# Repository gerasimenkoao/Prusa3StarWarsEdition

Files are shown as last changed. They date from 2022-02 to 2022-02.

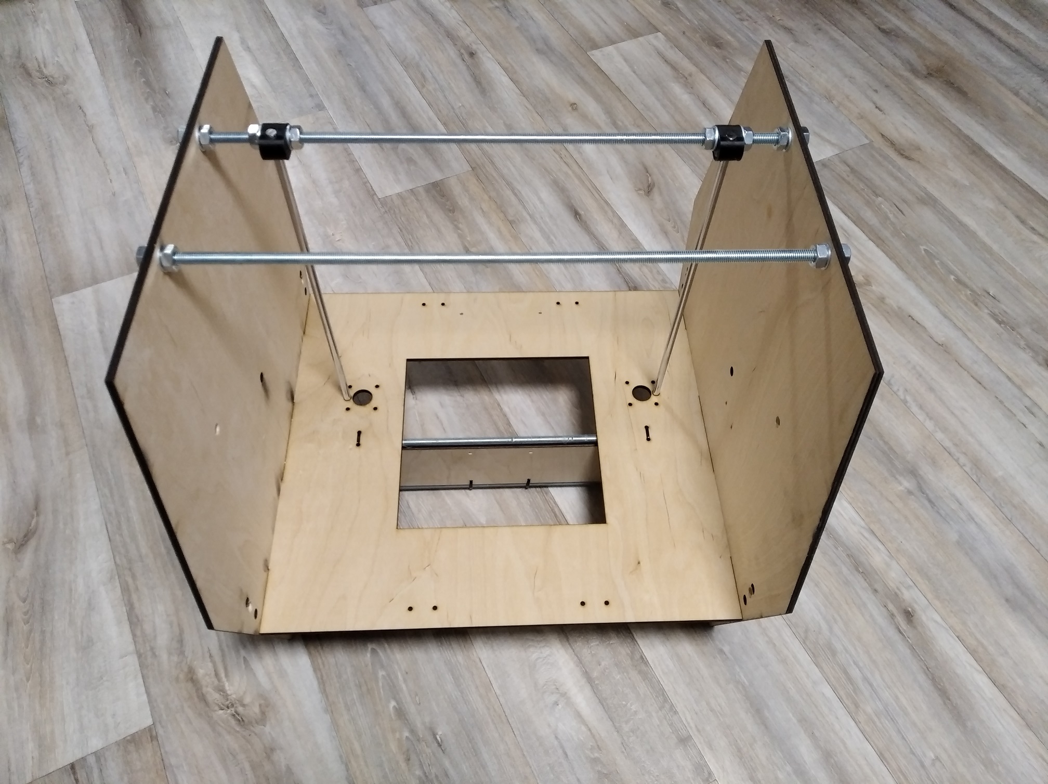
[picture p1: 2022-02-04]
photos/02frameBuild.jpg

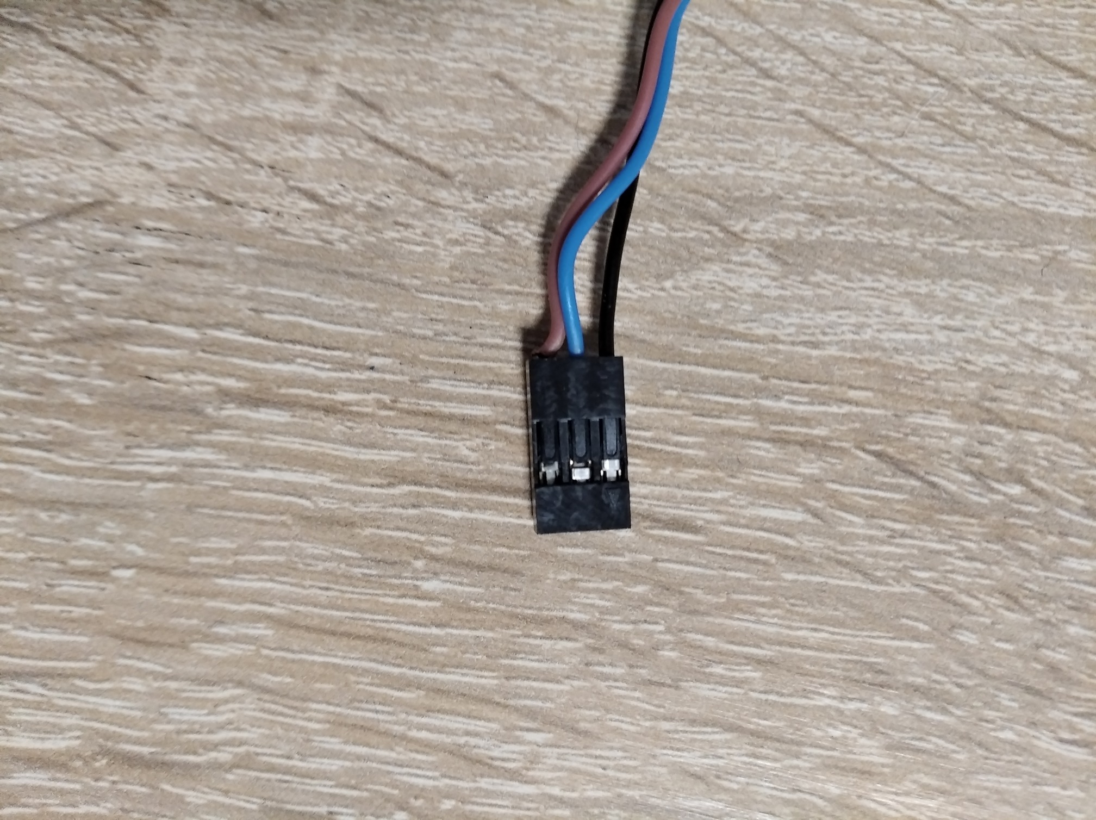
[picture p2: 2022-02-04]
photos/19LJ12A3-4-Z-BY PNP wiring.jpg

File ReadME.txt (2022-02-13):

Prusa i3 StarWars edition
TIE Figter frame build manual (can be easy installed dual extruder)

! X&Y axis same as in original printer (see prusa i3 build manual v1.0)
! Z-axis smooth rods is longer than i3 system. 

Present system use E3D V6 bowden exruder, RAMPS 1.6 board and LCD1604 control panel & 400W ATX power supply.
19LJ12A3-4-Z-BY PNP inductive proximity sensor also can be needed instead of Z-axis endstop.

All printed parts placed in /stls folder
Original printed parts named TIEFighter*
Dimension of hotend mount need be multiplied x10

Drawings 4 laser cutting from 6mm plywood placed in /cad folder
TIEFighter1x have size 482x520mm
TIEFighter2x - two side with size 500x500mm
All elements can be cutted from 500х1250 sheet of plywood (20x60inch)
Inner size between sides is 470mm.
The shelf is asymmetrical - motors and rods shifted to the right at 5mm - mount it carefully!

Also 4 bulding frame needed next parts:

Threaded rod M10, 50cm (4x) 
Threaded rod M10, 44cm (2x)

Threaded rod M8, 50cm (4x)

Y-axis smooth rod  8mm, 420mm (2x)
X,Z-axis smooth rod  8mm, 375mm (4x)

Two 80mm screw 4 filament coil holder with width of 60mm.

M10 Nut (30x)
M10 Washer (30x)  
M8 Nut (40x) 
M8 Washer (40x) 

White adhesive tape 16-19mm width

Black spray paint - 3х 400gramm can.

steel 4.5mm BB ball from airgun - 2x (optional)

1000mm 12V white led stripe connected to power
1000mm 12V red led stripe connected to hotend heater line

Any other&small parts same as in original Prisa i3

Building sequence shown in numbered photos (/photos folder)

And may the Force be with you.

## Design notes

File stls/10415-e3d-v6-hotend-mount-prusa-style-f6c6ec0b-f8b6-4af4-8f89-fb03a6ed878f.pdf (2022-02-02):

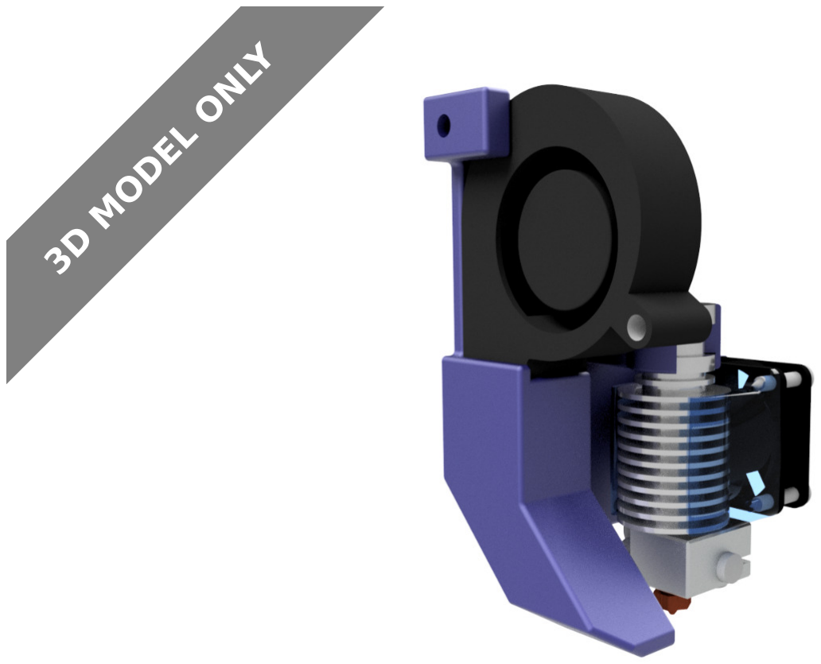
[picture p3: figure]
3D MODEL ONLY

## Summary

UPDATED version to be found on: https://www.thingiverse.com/thing: 3462260

This is an mount for the e3d v6 hotend or clones. This mount is designed in such a way that it is possible to print in one go.

The mount should be 'the' all in one solution with minimal fastners for this popular printer and hotend style. The hotend should just 'snapon'!

The mount has been designed for an x axis distance of 45mm. If any other sizes are desired be sure to let me know in the comments.

This design is still a work in progress. We are working hard on a new and improved version with support for an end stop, cable management, and belt connecting capabilities. Be sure to check back in 2-3 weeks! Pictures of assembled mount will also be published!

3D Printers (https://www.prusaprinters.org/prints?categoryId=1) > 3D Printers - Upgrades (https://www.prusaprinters.org/prints?categoryId=2)

## Category: 3D Printer Parts Print Settings

Printer Brand: Anet

Printer: A8

Rafts: No

V (https://www.prusaprinters.org/social/2836/prints) Vatuhiva (https://www.prusaprinters.org/social/2836/prints)

## e3D v6 hotend mount prusa style

VIEW IN BROWSER (https://www.prusaprinters.org/prints/10415-e3d-v6-hotend-mount-prusa-style)

updated 14. 11. 2019 | published 14. 11. 2019

Model Files (.stl, .3mf, .obj, .amf) | DOWNLOAD ALL FILES (https://www.prusaprinters.org/prints/10415-e3d-v6-hotend-mount-prusa-style/files)

120.0 KB
updated 14. 11. 2019 | (https://www.prusaprinters.org/prints/10415-e3d-v6-hotend-mount-prusa-style/files)

Supports: No

Resolution: 0.15

Infill: 20-30%

## Standards

NGSS

Find source .stl files on Thingiverse.com (https://www.thingiverse.com/thing:3362682)

The Author has not uploaded any G-codes.
Try to search in User G-codes (https://www.prusaprinters.org/prints/10415-e3d-v6-hotend-mount-prusa-style/user-gcodes) section or generate and upload your own.

## License

This work is licensed under a
Creative Commons (4.0 International License)

Attribution (http://creativecommons.org/licenses/by/4.0/)

✖ | Sharing without ATTRIBUTION
✔ | Remix Culture allowed
✔ | Commercial Use
✔ | Free Cultural Works
✔ | Meets Open Definition

e3d_bowden_hotend_mount.stl

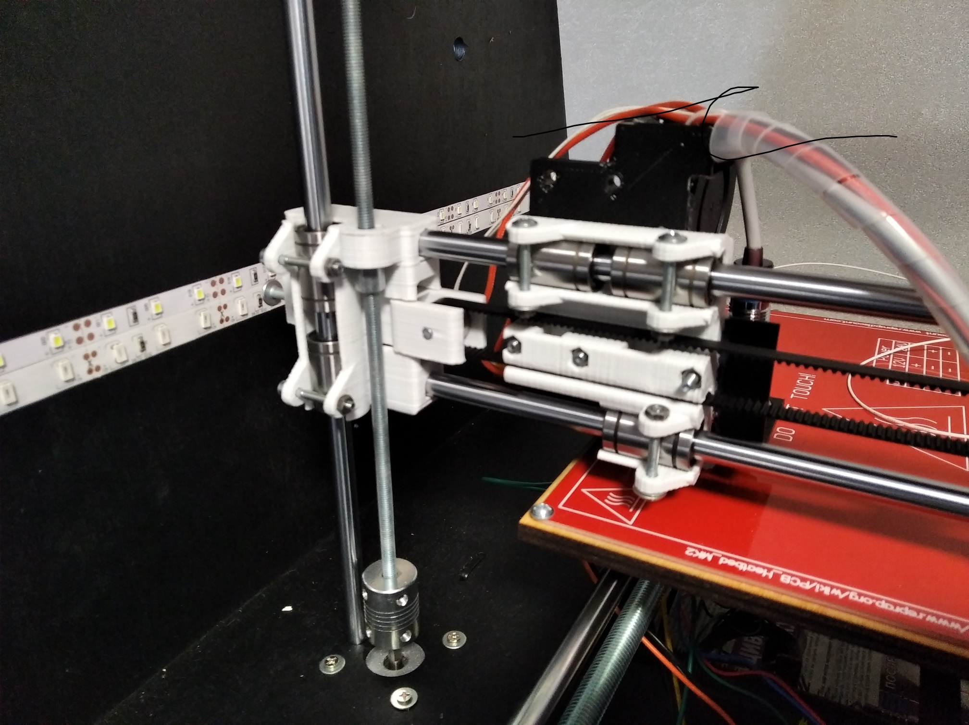
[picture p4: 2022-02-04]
photos/18ZXaxisMout.jpg

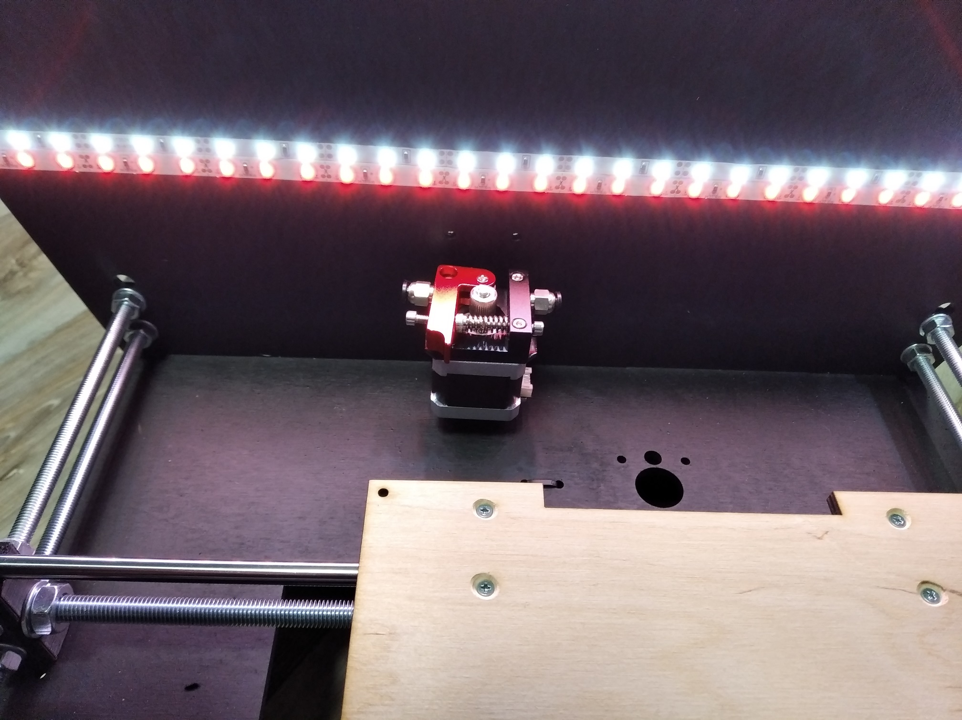
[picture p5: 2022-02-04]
photos/12LEDstrip.jpg

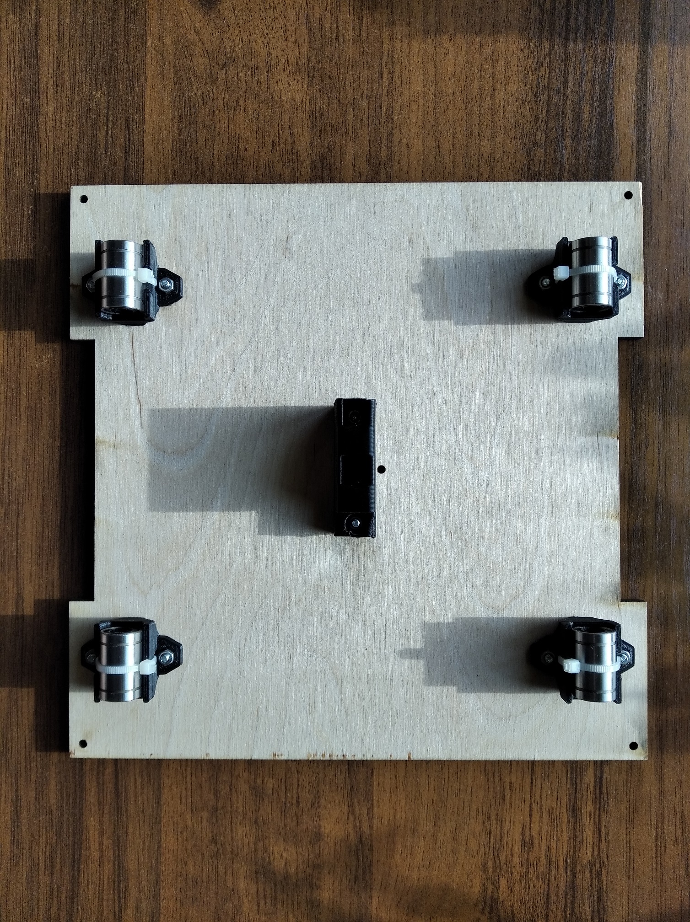
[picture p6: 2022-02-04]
photos/11YbearingMount.jpg

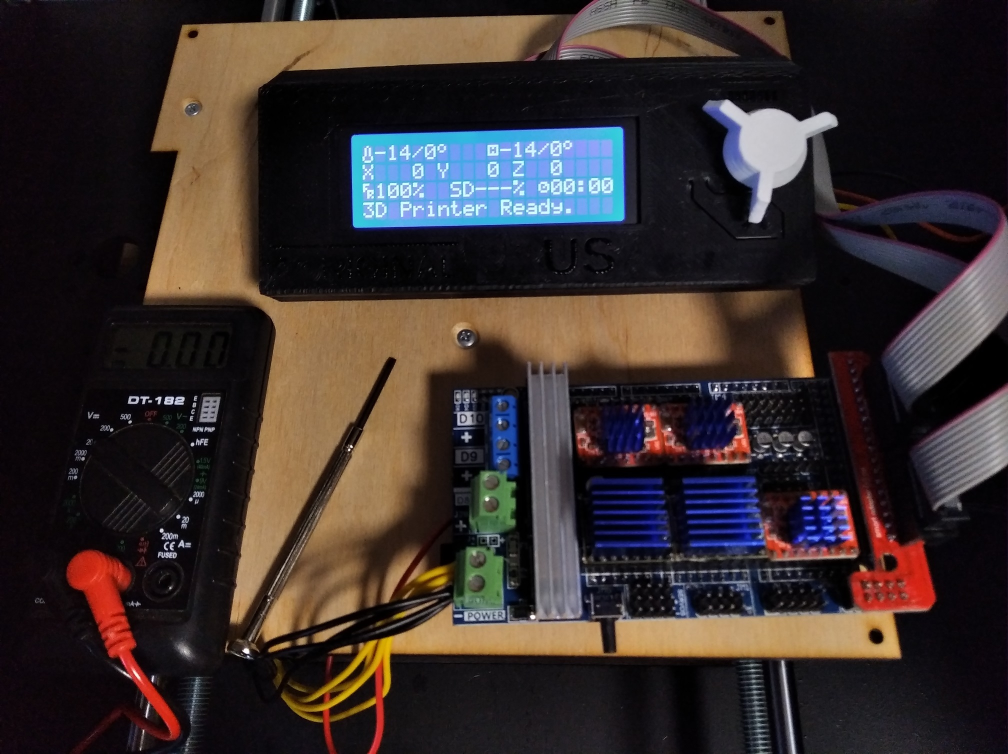
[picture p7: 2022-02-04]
photos/14driverCurrentAdjust.jpg

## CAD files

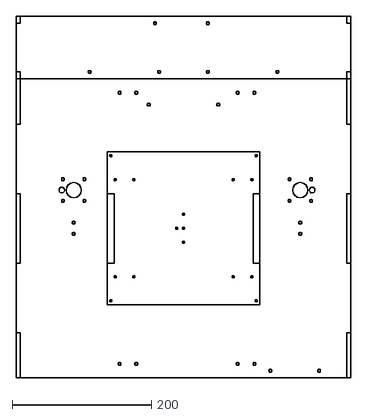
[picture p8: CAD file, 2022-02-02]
cad/TIEFighter1x.dxf
482.0 x 520.0

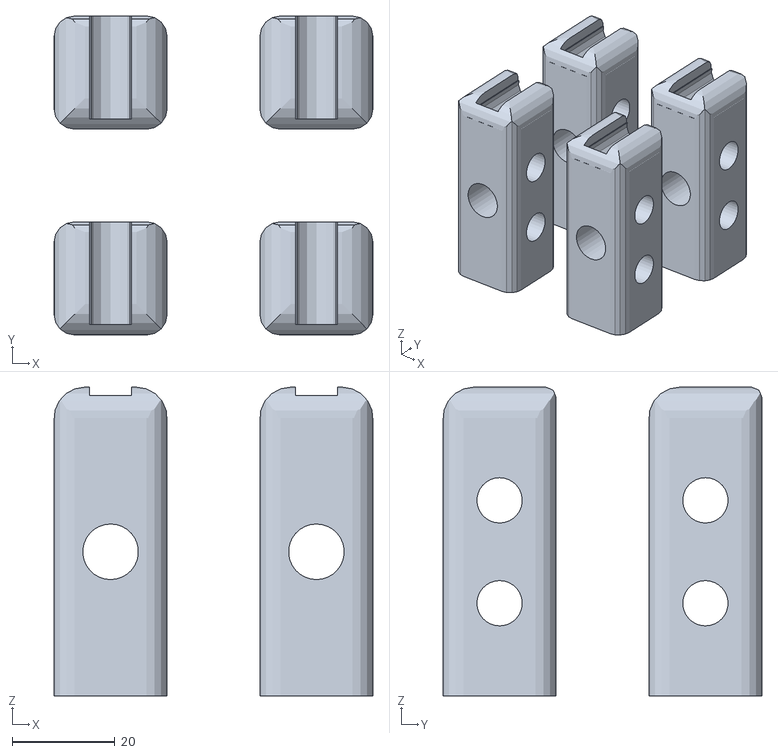
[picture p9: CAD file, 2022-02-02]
stls/y-axis-corner.stl
62.0 x 62.0 x 60.0

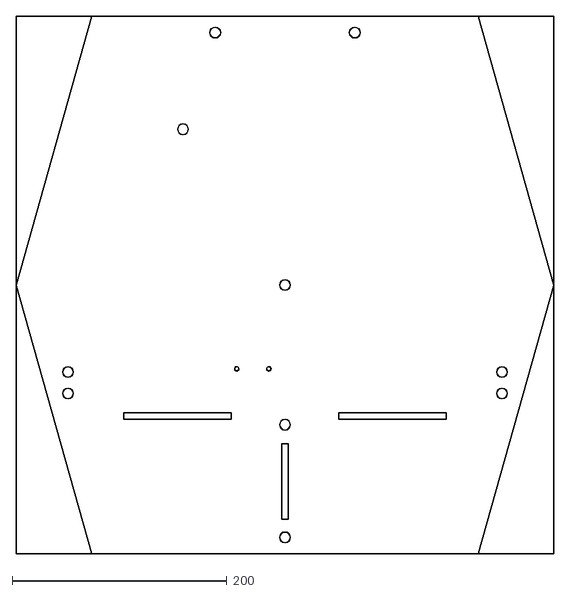
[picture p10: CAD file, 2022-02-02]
cad/TIEFighter2x.dxf
500.0 x 500.0

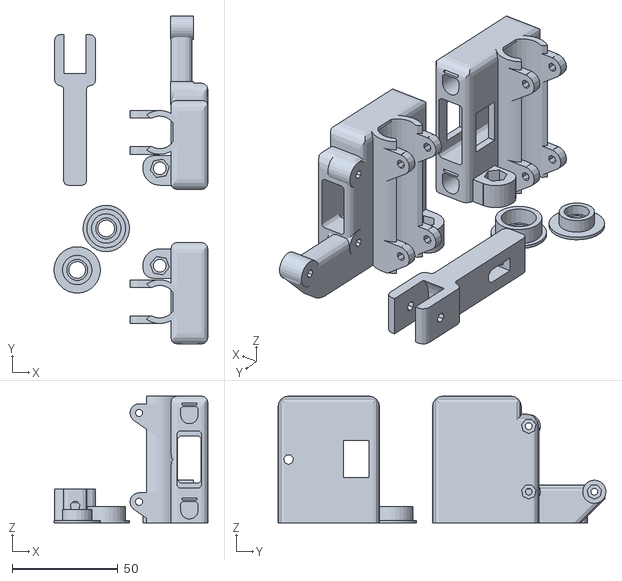
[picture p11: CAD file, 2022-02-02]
stls/x-end.stl
72.7 x 155.0 x 60.0

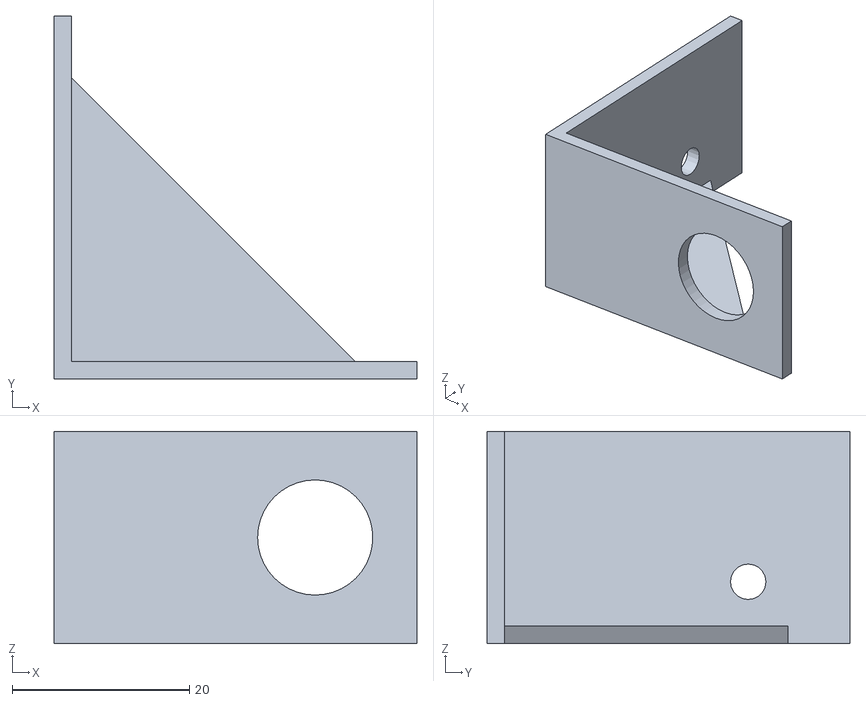
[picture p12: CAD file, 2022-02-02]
stls/TIEFighterSensorHolder.stl
41.0 x 41.0 x 24.0

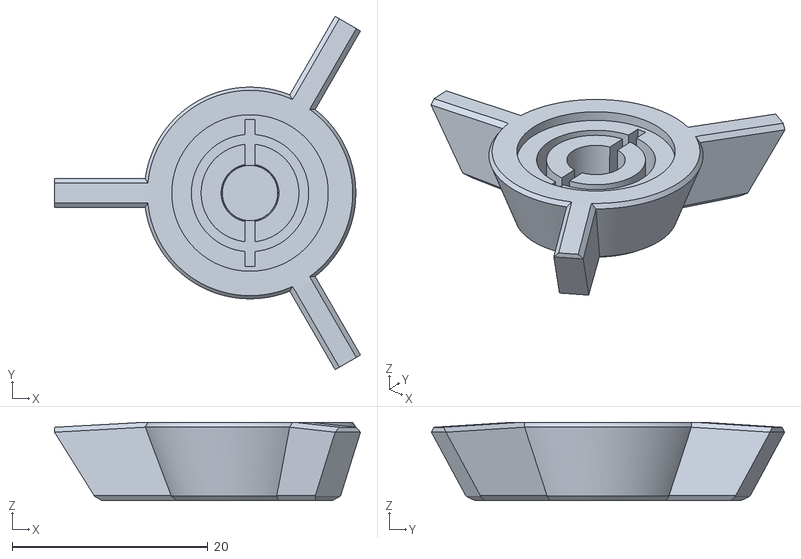
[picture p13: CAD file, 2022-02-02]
stls/LCD-knob.stl
31.3 x 36.1 x 8.00

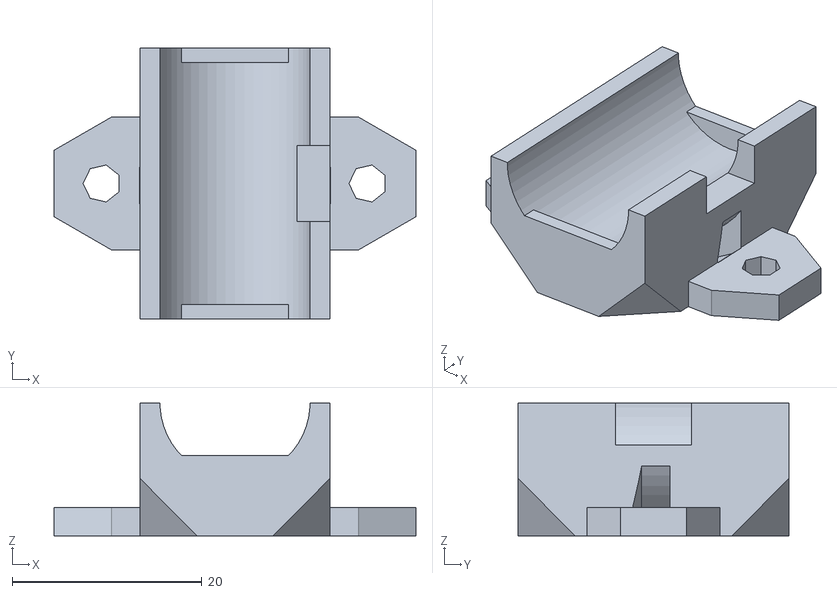
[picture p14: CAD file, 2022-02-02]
stls/y-bushing_1x.stl
38.1 x 28.5 x 14.0

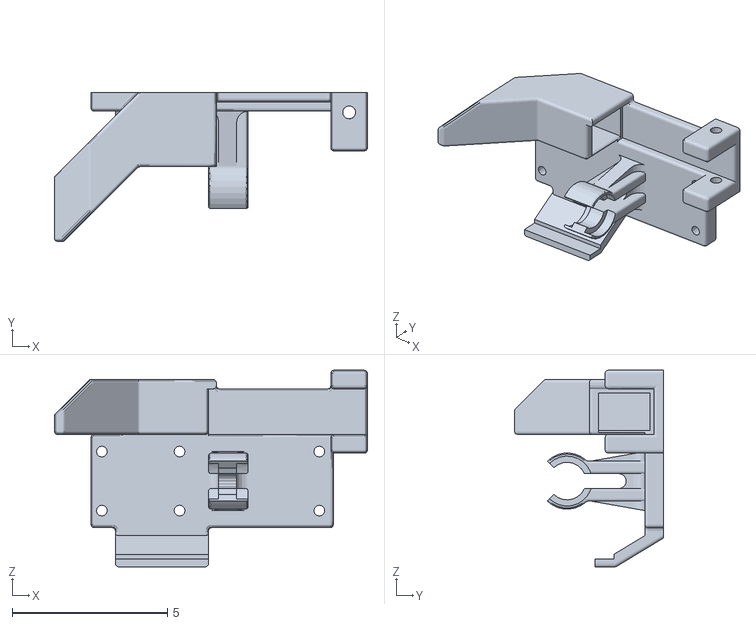
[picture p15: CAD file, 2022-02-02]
stls/e3d_bowden_hotend_mount10x.stl
10.1 x 4.79 x 6.33

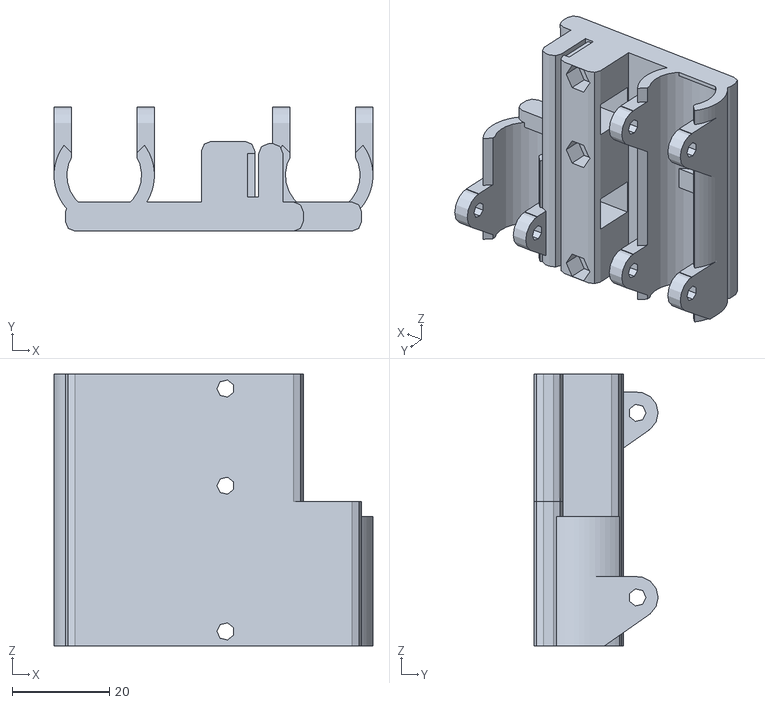
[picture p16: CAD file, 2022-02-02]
stls/x-carriage.stl
65.7 x 25.6 x 56.0

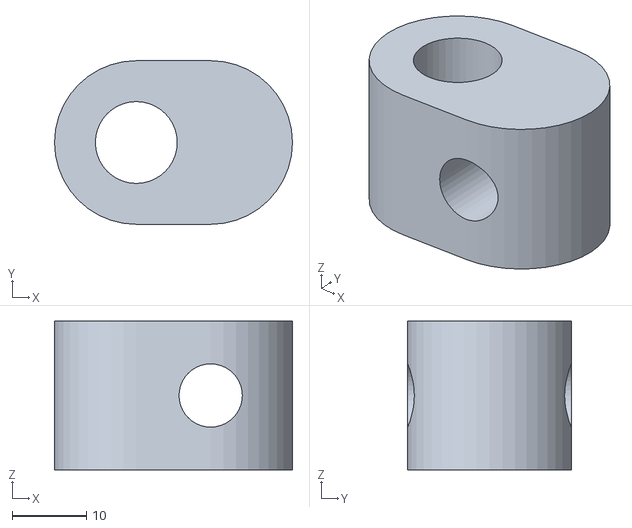
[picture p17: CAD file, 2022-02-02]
stls/TIEFighterZholder.stl
32.0 x 22.0 x 20.0

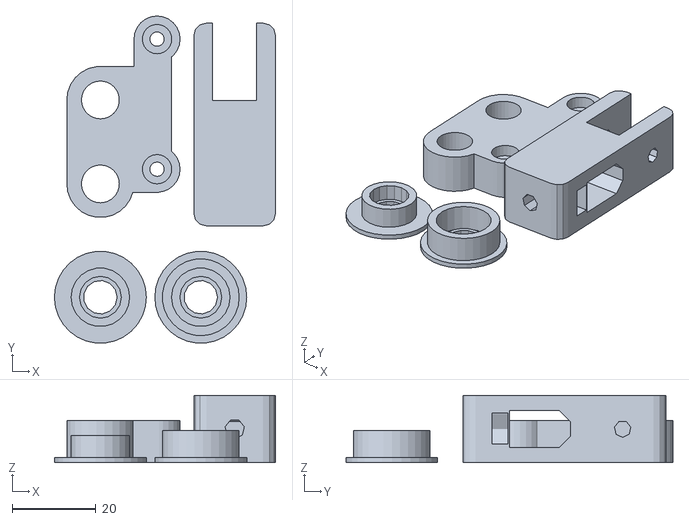
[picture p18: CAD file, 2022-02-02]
stls/y-drivetrain.stl
52.7 x 77.9 x 16.0

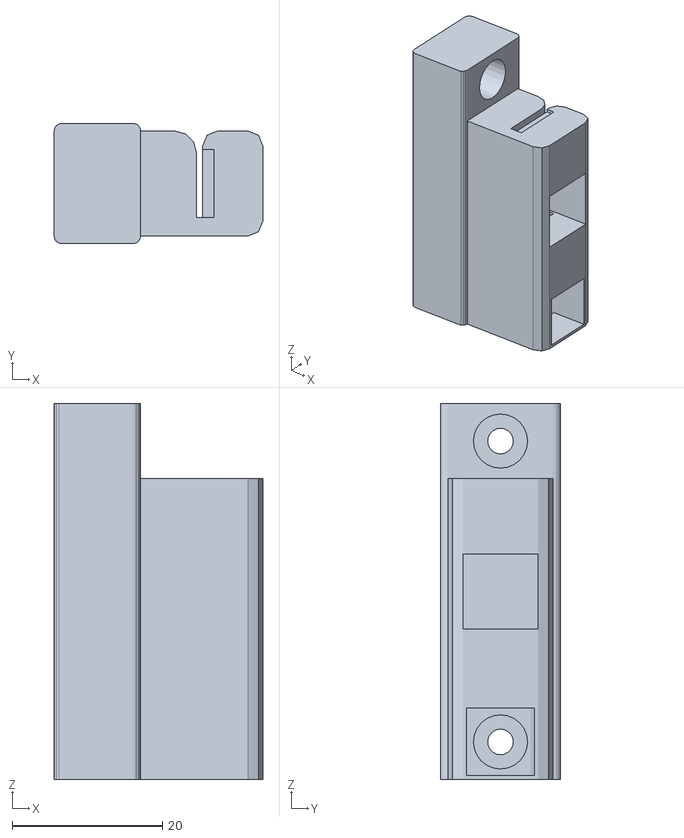
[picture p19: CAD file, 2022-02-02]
stls/y-belt-holder.stl
27.8 x 16.0 x 50.0

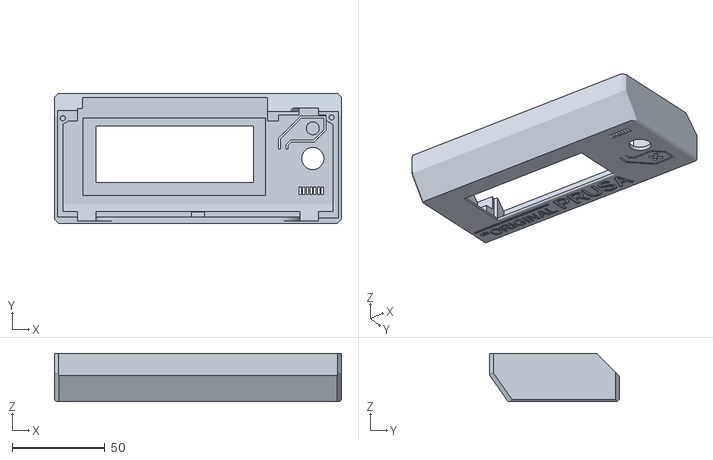
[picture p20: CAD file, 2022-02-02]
stls/LCD-cover-ORIGINAL.stl
155.0 x 70.0 x 26.0

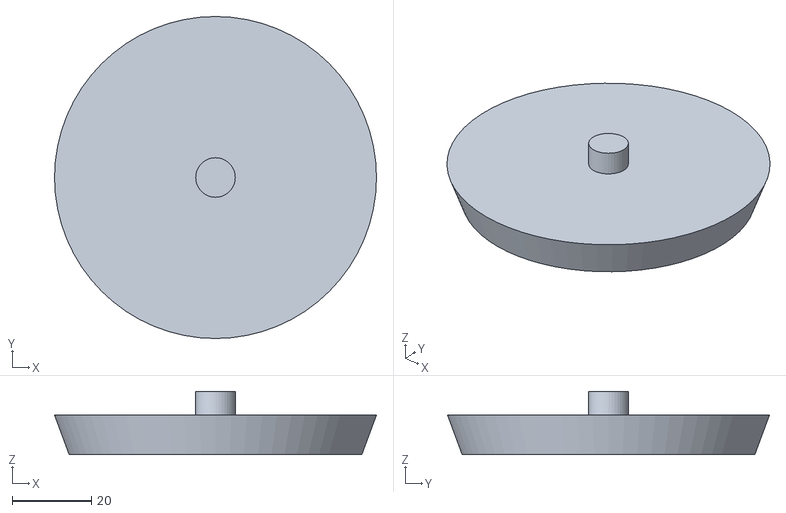
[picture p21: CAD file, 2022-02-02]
stls/TIEFighterSideCap.stl
81.4 x 81.4 x 16.0
